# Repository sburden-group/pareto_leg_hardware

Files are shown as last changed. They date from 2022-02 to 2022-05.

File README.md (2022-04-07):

# Pareto Leg Hardware

contains all hardware (and control software) designs for the Pareto Leg

## Setup
Getting your environment ready to talk to some robot legs will involve:
1. provisioning your computer
1. provisioning the ODrive with the right firmware
1. calibrating the ODrive motors
1. Assembling the leg hardware
1. Wiring the leg electronics
1. Setting the zero point for each leg element

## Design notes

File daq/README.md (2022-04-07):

The "DAQ" is a separate device for measuring current.
It is installed in series into the power supply of the source (ODrive board in this case) to be measured.
Data is sampled at 5[KHz] and streamed in real time to a python script, which aggregates the data and writes it to a CSV file.

The DAQ is just a 1bitsy and a [ACHS-7124](https://www.pololu.com/product/4033)an analog in-series current measurement sensor.
A voltage divider that maps the input from 0-to-5 to 0-to-3.3 is also present.

## Usage

To start collecting data, use the **acquire\_data.py** script.
````
./acquire_data.py --seconds=3
````

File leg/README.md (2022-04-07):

# Pareto Leg Hardware
This is a CAD snapshot (Solidworks 2020) of the Pareto Leg.

## Summary
This model is modeled "[Top-Down](https://help.solidworks.com/2018/english/SolidWorks/sldworks/c_Top-Down_Design_Overview.htm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,moves%20down%20to%20the%20parts.)," where most of the structural parts are driven from parameters in *main\_body\_sketch.SLDPRT*.
The advantage is that variables can be tweaked from one file, and the rest of the top assembly will resize to accommodate the changes.
The top assembly also contains several *Configurations* with predefined parameters that will resize the model to create a particular leg instance.

If you need to make model changes, follow the guidelines in [editng_the_cads.md](./editing_the_cads.md)

# Fabrication Notes

## Fabrication Tools
* Drill Press
* 7mm Carbide Drill bit, [McMaster-Carr](https://www.mcmaster.com/3030A34/)
* Handheld Pipe Cutter, [McMaster-Carr option](https://www.mcmaster.com/pipe-cutters/metal-tube-and-conduit-cutters-8/)
* Soldering iron (for installing heat set inserts)
* Soldering iron Heat Set Insert Installation Tip, [Amazon](https://www.amazon.com/Heat-Set-Inserts-Compatible-SP40NKUS-Connecting/dp/B08B17VQLD)

## Stainless Steel Parts
Flat stainless steel parts (spring anchors) need to be sourced externally.
All spring anchors can be fabricated externally from [SendCutSend](https://sendcutsend.com/).
Simply import a DXF and specify *0.8mm thick 304 Stainless Steel* as the material.
(Pricing is ~$30 for about 10 spring anchors, and turnaround time is about 1 week.)

## Carbon Fiber Parts
Carbon Fiber Parts need to be sourced externally.
All carbon fiber parts can be fabricated externally from [CNCMadness.com](https://cncmadness.com/).
Just send him a DXF and specify *6mm plain weave carbon fiber*.
(Pricing is < $200 for two leg setups, and turnaround time is about 1 week.)

### Post-Processing
Parts from CNC Madness will need to be touched up before they can be used.
Specifically, the holes need to be cleaned up with a 7mm drill bit and a 5mm bushin needs to be installed in each joint hole.

### Warnings:
Carbon fiber is both sharp and very abrasive.
It can be wet-sanded to reduce the risk of injuring people who run their hands along the edge.
You must use carbide tooling to work with carbon fiber.
Conventional high speed steel tools will dull immediately.

## 3D Printed Parts

### Printed Part Settings
Print the following parts with these settings.
Note that exceptions exist, though.
See the notes for exceptions to these settings.

* 0.2mm or 0.24mm thick layer lines
* PLA or HTPLA
* print in the provided STL orientations
* 6 perimeter layers (This is critical especially for parts with inserts)
* No support material

| **Qty** | **Part Link** | **Notes** |
|:---:|:---:|:---:|
| 1 | [Foot](./fabrication_exports/stls/foot.STL) | Print with ~20 perimeter layers to create a solid object. Print from something more impact resistant than PLA, perhaps [CF HTPLA](https://www.proto-pasta.com/products/light-grey-carbon-fiber-composite-htpla). |
| 1 | [Threaded Foot Tip](./fabrication_exports/stls/threaded_foot_tip.STL) | Print from TPU or something rubbery |
| 2 | [Knee Bumper](./fabrication_exports/stls/knee_bumpter.STL) | |
| 2 | [Pogo Bearing Spacer](./fabrication_exports/stls/pogo_bearing_spacer.STL) | |
| 2 | [Knee Spring Anchor](./fabrication_exports/stls/knee_bumper.STL) | |
| 2 | [Pogo Center Tabs](./fabrication_exports/stls/pogo_center_tab.STL) | |
| 2 | [Pogo Center Tube Retainer](./fabrication_exports/stls/pogo_center_tube_retainer.STL) | can also be laser cut from 3.175mm Delrin sheet |
| 2 | [Inc Encoder Shaft Adaptor](./fabrication_exports/stls/inc_encoder_shaft_adaptor.STL) | can also be laser cut from 3.175mm Delrin sheet. Only needed if using AMT102-V encoders. |
| 2 | [Inc Encoder Shaft](./fabrication_exports/stls/incremental_encoder_shaft.STL) | Print *with* support material. Only needed if using AMT102-V encoders. |
| 8 | [M3 8mm Spacer](./fabrication_exports/stls/8mm_m3_spacer.STL) | |
| 1 | [Base Plate](./fabrication_exports/stls/base_plate.STL) or [No-Knee Springs Base Plate](./fabrication_exports/stls/base_plate_no_knee_springs.STL) | two different sizes depending on if the design uses knee springs or not. |

### Post Processing
The Foot Piece needs to have its 7mm hole drilled out, and then two 5mm bushing need to be pressed in, one from either end.
(You can use the same 7mm carbon fiber drill bit also used on the carbon fiber parts.)

## (3D Printed) Parts with Inserts
Some parts need heat-set inserts installed into them.
To install these, use a soldering iron with a heat-set insert tip and follow the [plate press technique](https://hackaday.com/2019/02/28/threading-3d-printed-parts-how-to-use-heat-set-inserts/).
Doing so should yield excellent surface finish with minimal blobbing.
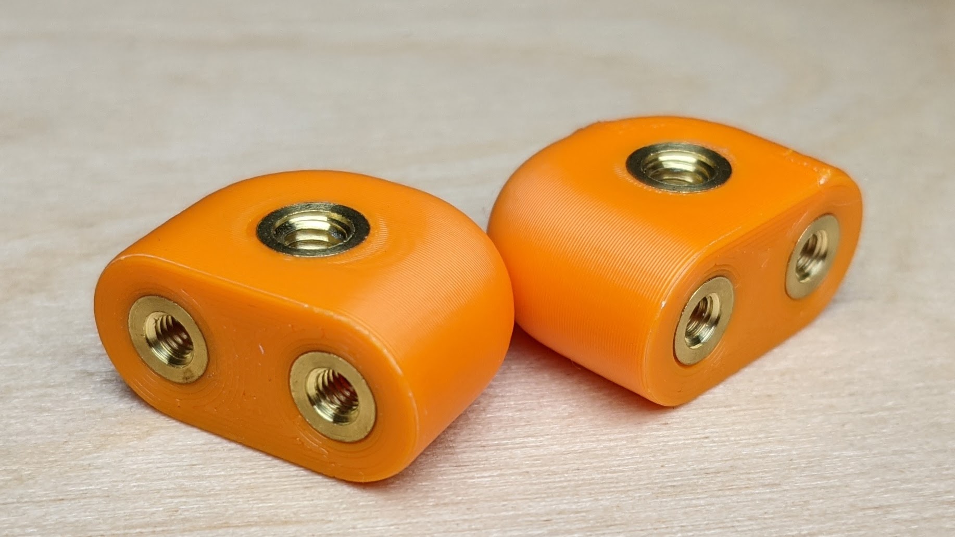
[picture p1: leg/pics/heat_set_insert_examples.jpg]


## Stainless Steel Guide Tube
This thin-walled tube comes from McMaster-Carr and can be cut to length with a pipe cutter. Length varies depending on design.
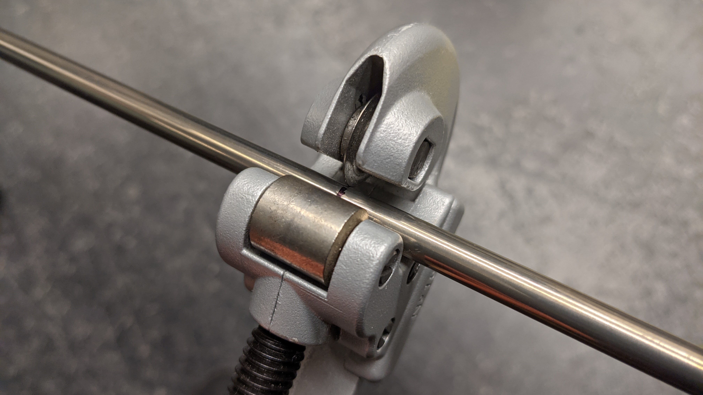
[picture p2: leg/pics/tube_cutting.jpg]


# Assembly
These robot legs can be assembled by you (or by some eager mechanically-curious undergrads).
For some of the finer details of the leg joint assembly, see [this doc](./knee_assembly_details.pdf).
For ordering more parts, see the [BOM](https://github.com/sburden-group/pareto_leg_hardware/blob/main/leg/no_spring_leg_bom%20L.pdf).

## Assembly Tools
You will need:
* 2mm Ball End Hex Key, [McMaster-Carr](https://www.mcmaster.com/5497A52/)
* 2.5mm Ball End Hex Key, [McMaster-Carr](https://www.mcmaster.com/5497A53/)
* 3mm Ball End Hex Key, [McMaster-Carr](https://www.mcmaster.com/5497A54/)
* 7mm Hex Nut Driver, [Amazon](https://www.amazon.com/gp/product/B000BQJ5ZY)

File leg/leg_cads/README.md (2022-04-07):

# CADs

This is a parametric assembly made with Solidworks 2020.
These files were exported with Solidworks' "Pack and Go" feature.

See the Assembly docs for info on sourcing stock parts, fabrication, and assembly.

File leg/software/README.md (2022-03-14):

## Folders
**Bringup Scripts** is for provisioning a new ODrive.

**lab\_experiments** is a "sketchbook" space for running lab experiments as scripts.

**leg\_control\_software** is the python package that enables control for the ODrive

**pareto-leg-control** is a Julia package for imposing particular dynamics on the robot in a control loop.

## Setup
**pareto-leg-control** is a separate Julia package with Python bindings installed as a submodule.
If you do not see it present as a directory, you need to download it with `git submodule init` followed by `git submodule update`.i

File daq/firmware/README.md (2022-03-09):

# Setup

## Required Hardware:
* breadboard
* [1bitsy](https://1bitsquared.com/products/1bitsy)
* [Black Magic Probe](https://www.adafruit.com/product/3839) for flashing
* Pololu In-Line Current Sensor, [+/- 40A](https://www.pololu.com/product/4033)

## Linux Development and Compiling Setup
* add the udev rules for (1) the black magic probe, (2) the 1bitsy custom usb device to your */etc/udev/rules.d* folder and then reload rules with `sudo udevadm control reload-rules`.
* Install gcc-arm-embedded according to the [libopencm3 guide](https://github.com/libopencm3/libopencm3#prerequisites)
* Pull the submodule repository in with: `git submodule init` and then `git submodule update`.
* cd into the **libopencm3** directory and build the code with `make`
* with libopencm3 built, you can now invoke the Makefile for this project in this directory with `make`

### Flashing
With the code compiled, you should be able to flash it with `make bmp-flash`.

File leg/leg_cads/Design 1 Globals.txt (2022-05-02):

"l2" = 191

"D3@Body Driving Dimensions" = "l2"

"l1" = 104

"D4@Body Driving Dimensions" = "l1"

"s1r" = 135deg

"s2r" = - 135deg

"offset"= 10mm

"s1_len" = 0mm

"s2_len" = 0mm

"s1_anchor_dist"= "offset" + "l1" + "s1_len"

"s2_anchor_dist"= "offset" + "l1" + "s2_len"'this was: = "offset" + "l1" + "s2_len"

"D5@Body Driving Dimensions" = "s1_anchor_dist"

"D6@Body Driving Dimensions" = "s2_anchor_dist"

"D7@Body Driving Dimensions" = "s1r"

"D8@Body Driving Dimensions" =  - "s2r"

"carbon_fiber_plate_thickness"=6

"motor_to_motor_spacing"=55.5

"D1@Sketch4"="motor_to_motor_spacing"

"D1@Boss-Extrude3"="l1"+"l2" + 8

"D1"= "motor_to_motor_spacing" + 30mm

"D10@Body Driving Dimensions"="offset"+5mm

"D12@Body Driving Dimensions"="offset"+5mm

"D4@side plate profile"="l1"+"offset"

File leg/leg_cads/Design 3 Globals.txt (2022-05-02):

"l2" = 182.421

"l1" = 87.579

"s1r" = 2.356194rad

"s2r"= - 135deg

"offset"= 10mm

"s1_len" = 76.2mm

"s2_len" = 0mm

"s1_anchor_dist"= "offset" + "l1" + "s1_len"

"s2_anchor_dist"= "offset" + "l1" + "s2_len"'this was: = "offset" + "l1" + "s2_len"

"carbon_fiber_plate_thickness"=6

"motor_to_motor_spacing"=55.5

"D1"= "motor_to_motor_spacing" + 30mm

"pogo_spacer_offset"= 15mm + 6.38mm

"cspring len" = 116.586

"cspring mult" = 2

"cspring_spacer_depth"= "l1" + "l2" - "cspring len" * "cspring mult" - "pogo_spacer_offset"

"D1@Boss-Extrude1"="cspring_spacer_depth"

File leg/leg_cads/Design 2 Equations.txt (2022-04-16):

"l2"= 185

"D3@Body Driving Dimensions" = "l2"

"l1"= 85

"D4@Body Driving Dimensions" = "l1"

"s1r"= 2.14212rad

"s2r"= - 2rad

"offset"= 15mm

"s1_len"= 0.08255m

"s2_len"= 0.015m

"s1_anchor_dist"= "offset" + "l1" + "s1_len"

"s2_anchor_dist"= "offset" + "l1" + "s2_len"'this was: = "offset" + "l1" + "s2_len"

"D5@Body Driving Dimensions" = "s1_anchor_dist"

"D6@Body Driving Dimensions" = "s2_anchor_dist"

"D7@Body Driving Dimensions" = "s1r"

"D8@Body Driving Dimensions" =  - "s2r"

"carbon_fiber_plate_thickness"=6

"D1@Tibya" = "carbon_fiber_plate_thickness"

"D1@Boss-Extrude2"="carbon_fiber_plate_thickness"

"motor_to_motor_spacing"=55.5

"D1@Sketch4"="motor_to_motor_spacing"

"D1@Boss-Extrude3"="l1"+"l2" + 8

"D1" = "motor_to_motor_spacing" + 30mm

"D1@Boss-Extrude12"="carbon_fiber_plate_thickness"

"D3@Sketch44"="s2_anchor_dist"/2

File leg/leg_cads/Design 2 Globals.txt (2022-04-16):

"l2"= 185

"l1"= 85

"s1r"= 2.14212rad

"s2r"= - 2rad

"offset"= 10mm

"s1_len"= 0.08255m

"s2_len"= 0.015m

"s1_anchor_dist"= "offset" + "l1" + "s1_len"

"s2_anchor_dist"= "offset" + "l1" + "s2_len"'this was: = "offset" + "l1" + "s2_len"

"carbon_fiber_plate_thickness"=6

"motor_to_motor_spacing"=55.5

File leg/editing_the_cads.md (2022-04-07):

# Editing The Model

Here's a quick walkthrough on exporting leg assemblies with custom dimenionsions.

## Configuraiton Overview
Many parts in the assembly are driven from a single part (`main_body_sketch.SLDPRT`) with many configurations, each of which has parameters set to different values.
The assembly itself also several configurations, each of which represent a different leg designs at a particular point in the design space.
This assembly configuration is built from parts pinned to a particular configuration.

## Tweaking Existing Leg Designs
Four Leg designs exist as separate configurations in the top assembly.

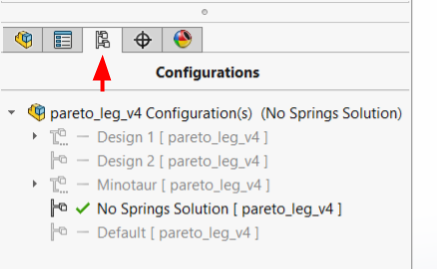
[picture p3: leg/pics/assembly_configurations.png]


To tweak an existing design's parameters, start by opening `main_body_sketch.SLDPRT`. Note that this part has configurations with names that match that of the corresponding assembly configuration.
To edit the equations that drive any configuration, right-click on *Equations* in the feature tree and select *Manage Equations*.

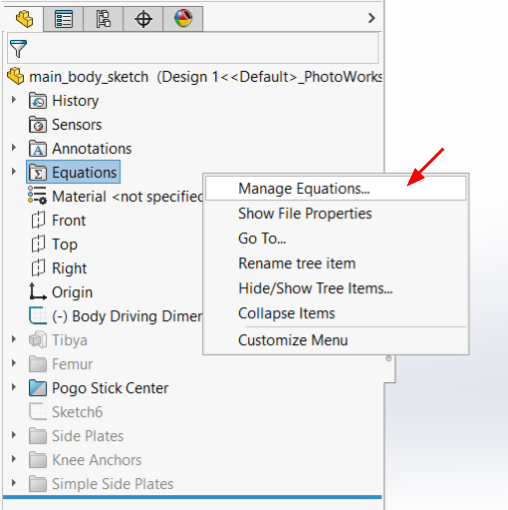
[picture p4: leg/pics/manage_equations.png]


This new window gives you direct edit access to parameters that drive the model.
Note that these parameters can be made to apply globally or be configuration-specific.
In pretty-much all cases, we want our parameter values to apply to be configuration-specific.

To edit a parameter, first ensure that the desired configuration is selected in the upper right corner and make sure that the variable value scope is set to *This Configuration*.

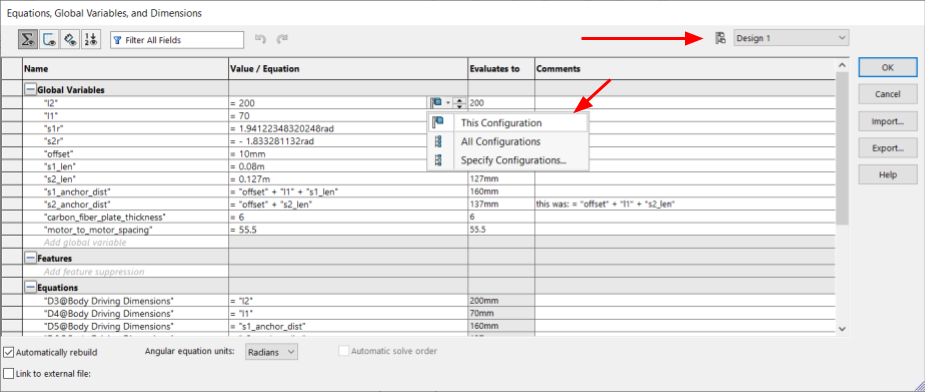
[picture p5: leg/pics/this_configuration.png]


Now you can just check *OK*, and the model configuration, and all derived configurations will apply the new value.
At this point, if you have the assembly open, it should prompt you about rebuilding the model.
If you say yes, the parts will resize.
If you save `main_body_sketch.SLDPRT`, these changes will take effect.

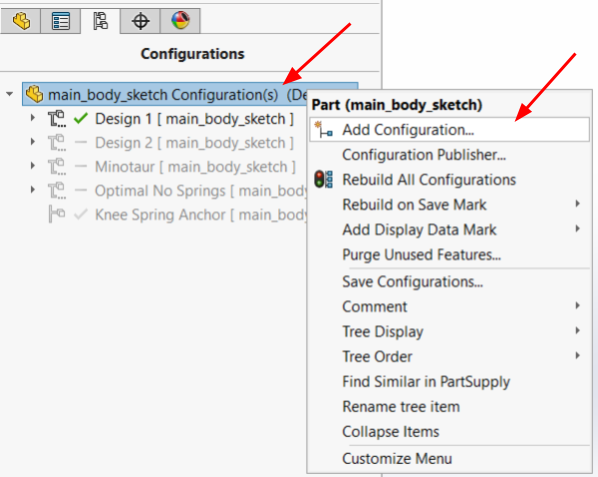
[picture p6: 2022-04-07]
leg/pics/new_configuration_part_level.png

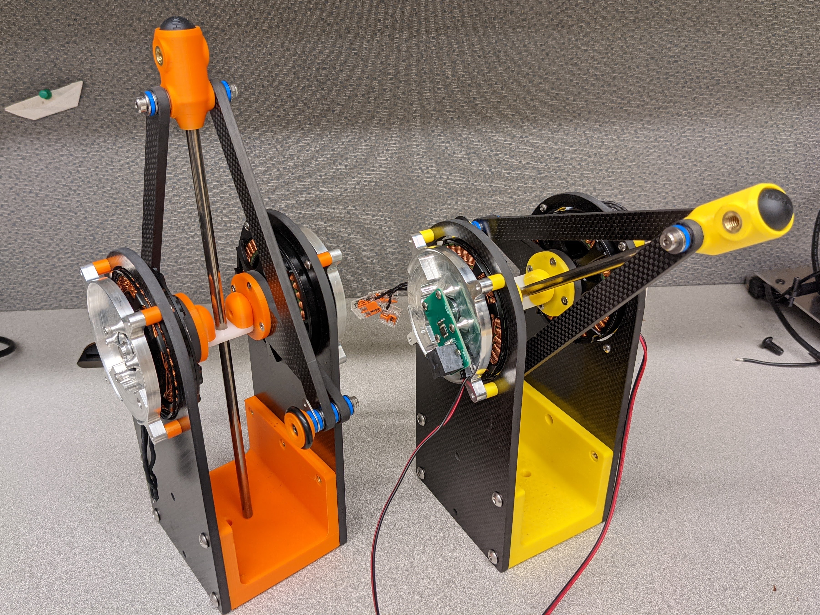
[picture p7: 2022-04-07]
leg/pics/pareto_leg_samples.jpg

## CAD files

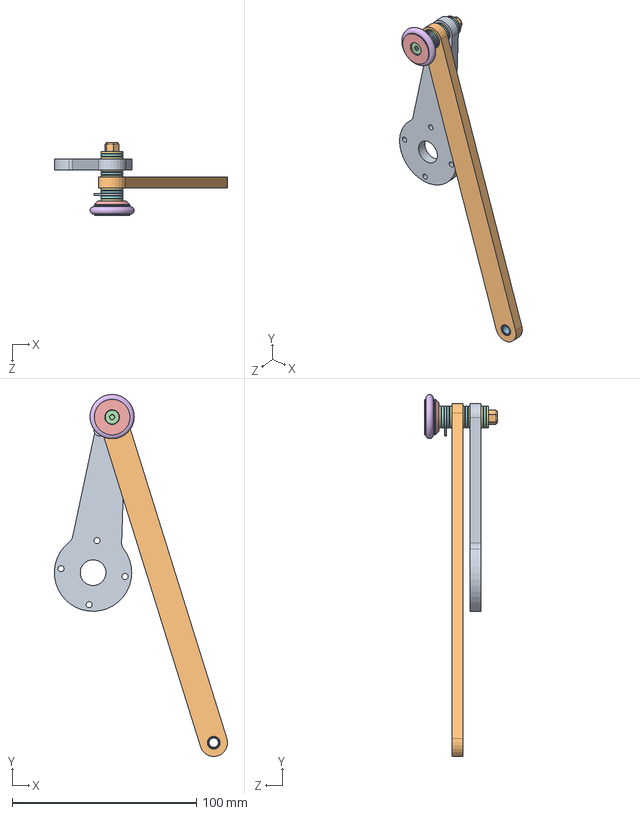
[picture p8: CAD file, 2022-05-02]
leg/leg_cads/half leg assembly v5.SLDASM
93.9 x 196.4 x 39.8 mm
Femur V5
Tibia v5
5mm_sleeve_bearing_6mm_long_7mm_od_MDZB5-6 x 3
m4_shoulder_screw_5mm_d_30mm_l_90278A376
knee_bumper_v4
9262K342-o-ring
m5_shim_1mm_thick_PCIMR5-12-1.0 x 6
thrust_bearing_5mm_bore_mtb-0512 x 4
Knee Anchor Loop
m4_locknut_93625A150

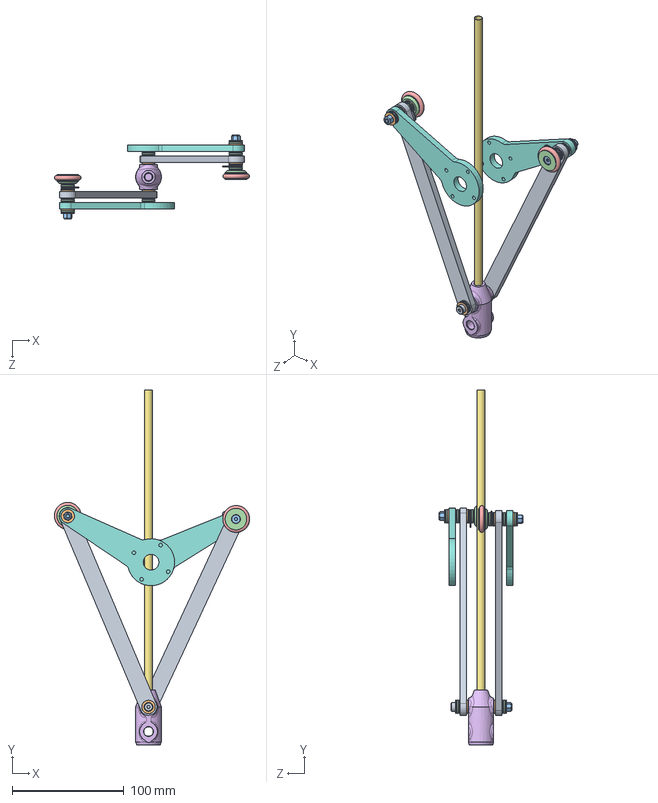
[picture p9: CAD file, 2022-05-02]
leg/leg_cads/full leg assembly v5.SLDASM
174.4 x 317.0 x 75.3 mm
m4_shoulder_screw_5mm_d_45mm_l_90278A507
m5_shim_1mm_thick_PCIMR5-12-1.0 x 18
m4_locknut_93625A150 x 3
thrust_bearing_5mm_bore_mtb-0512 x 10
5x11x4_flanged_bearing_57155K571 x 2
foot_v4
Pogo stick v5
Femur V5 x 2
Tibia v5 x 2
5mm_sleeve_bearing_6mm_long_7mm_od_MDZB5-6 x 6
m4_shoulder_screw_5mm_d_30mm_l_90278A376 x 2
knee_bumper_v4 x 2
9262K342-o-ring x 2
Knee Anchor Loop x 2

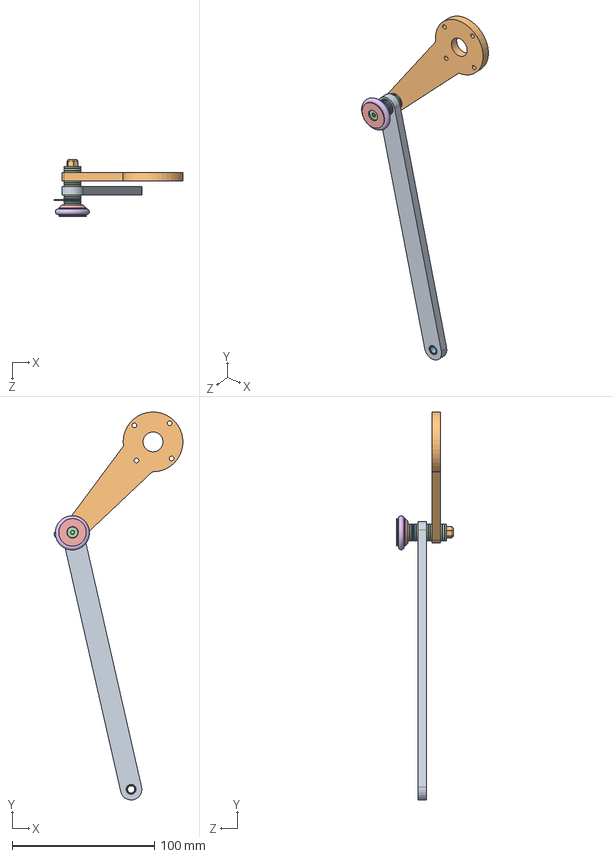
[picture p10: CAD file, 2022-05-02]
leg/leg_cads/Leg Assembly V5.SLDASM
90.3 x 272.4 x 39.8 mm
Femur V5
Tibia v5
5mm_sleeve_bearing_6mm_long_7mm_od_MDZB5-6 x 3
m4_shoulder_screw_5mm_d_30mm_l_90278A376
knee_bumper_v4
9262K342-o-ring
m5_shim_1mm_thick_PCIMR5-12-1.0 x 6
thrust_bearing_5mm_bore_mtb-0512 x 4
Knee Anchor Loop
m4_locknut_93625A150

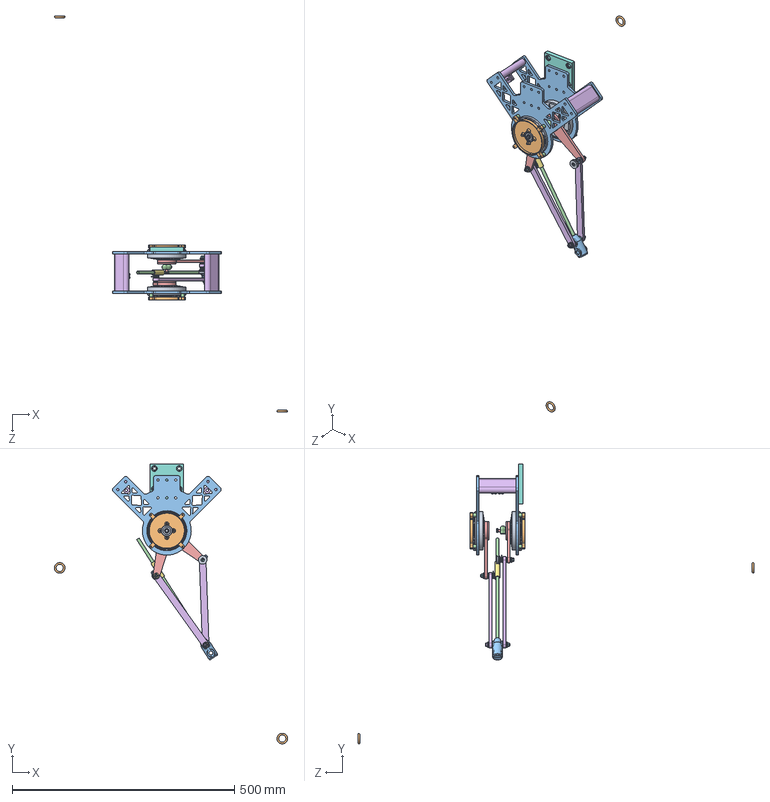
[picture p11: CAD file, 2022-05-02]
leg/leg_cads/Full Robot Assembly V5.SLDASM
524.9 x 629.8 x 891.1 mm
DYS 8108 x 2
motor_plate x 2
Side plate v5 x 2
8mm_spacer x 8
pogo_bearing_spacer x 2
m4_shoulder_screw_5mm_d_45mm_l_90278A507
m5_shim_1mm_thick_PCIMR5-12-1.0 x 18
m4_locknut_93625A150 x 3
thrust_bearing_5mm_bore_mtb-0512 x 10
5x11x4_flanged_bearing_57155K571 x 4
foot_v4
Pogo stick v5
Femur V5 x 2
Tibia v5 x 2
5mm_sleeve_bearing_6mm_long_7mm_od_MDZB5-6 x 6
m4_shoulder_screw_5mm_d_30mm_l_90278A376 x 2
knee_bumper_v4 x 2
9262K342-o-ring x 2
Knee Anchor Loop x 2
pogo_center
m4_shoulder_screw_5mm_d_5mm_l_90265A126 x 2
Knee Anchor V5 x 2
cspring_spacer
mounting bracket

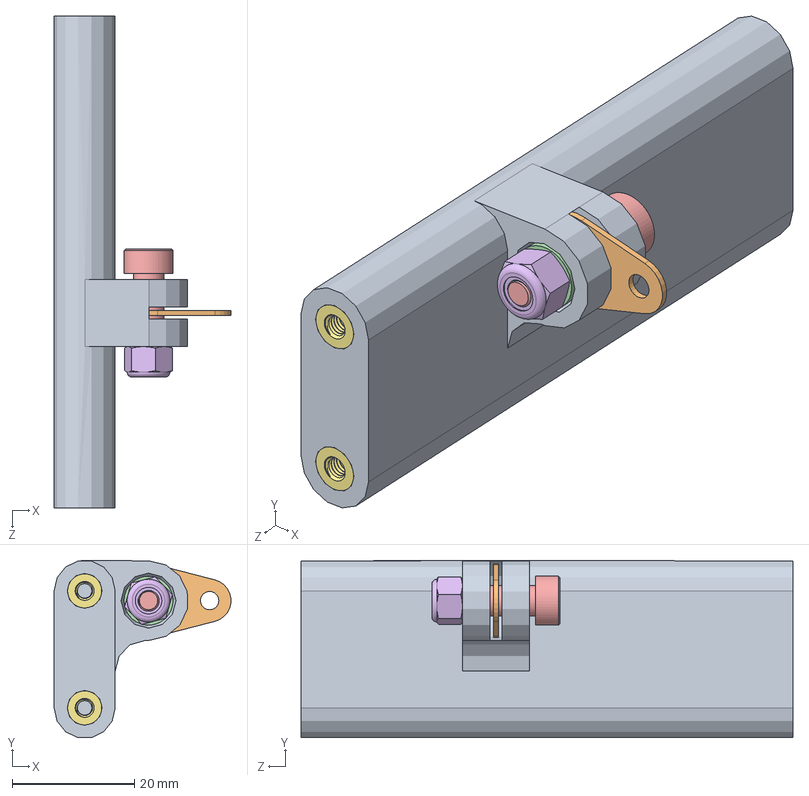
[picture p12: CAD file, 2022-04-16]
leg/leg_cads/knee_anchor_assembly.SLDASM
28.9 x 29.0 x 80.5 mm
main_body_sketch
knee_spring_anchor
4mm_sleeve_bearing_3mm_long_8mm_od_6658K114
5mm_sleeve_bearing_4mm_long_8mm_od_6658K116
m4_shoulder_screw_5mm_d_12mm_l_90278A371
m4_locknut_93625A150
m3_heat_set_insert_94180A331 x 4

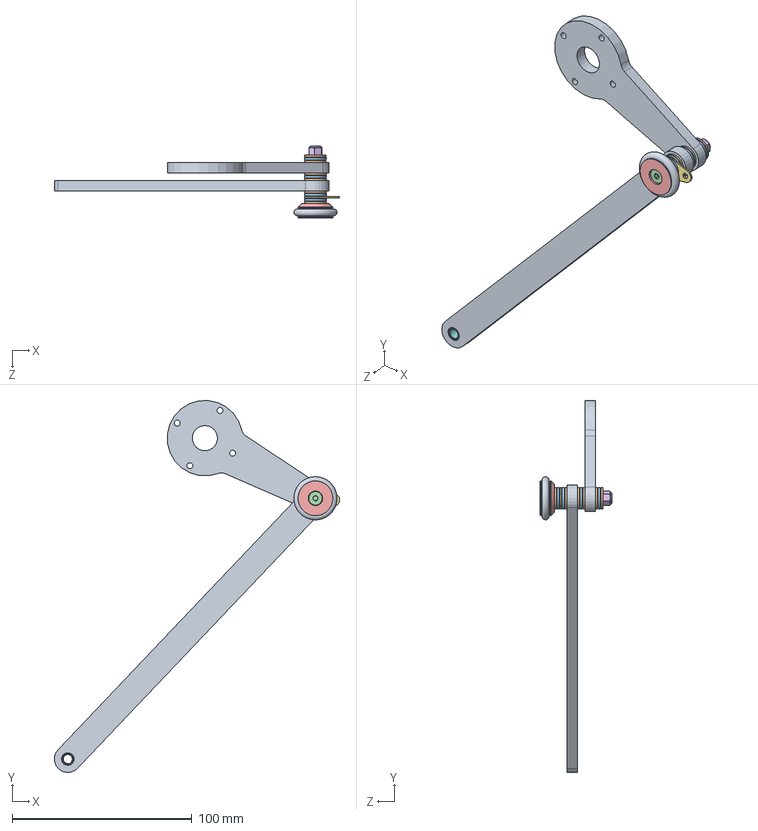
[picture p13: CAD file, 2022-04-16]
leg/leg_cads/leg_assembly.SLDASM
158.7 x 206.9 x 39.8 mm
main_body_sketch x 2
m5_shim_1mm_thick_PCIMR5-12-1.0 x 6
thrust_bearing_5mm_bore_mtb-0512 x 4
m4_shoulder_screw_5mm_d_30mm_l_90278A376
knee_bumper_v4
m4_locknut_93625A150
knee_spring_anchor
5mm_sleeve_bearing_6mm_long_7mm_od_MDZB5-6 x 3
9262K342-o-ring

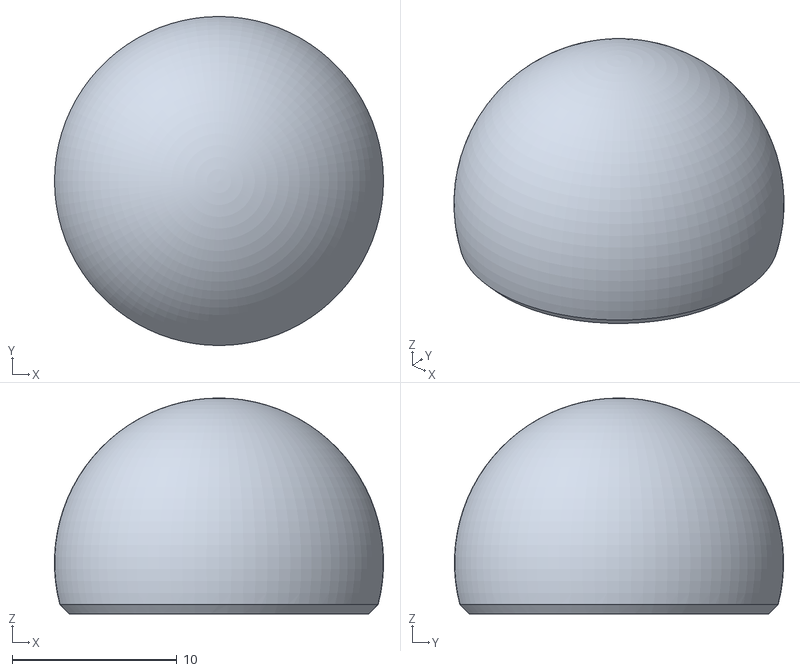
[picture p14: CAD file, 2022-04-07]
leg/fabrication_exports/stls/threaded_foot_tip.STL
20.0 x 20.0 x 13.1

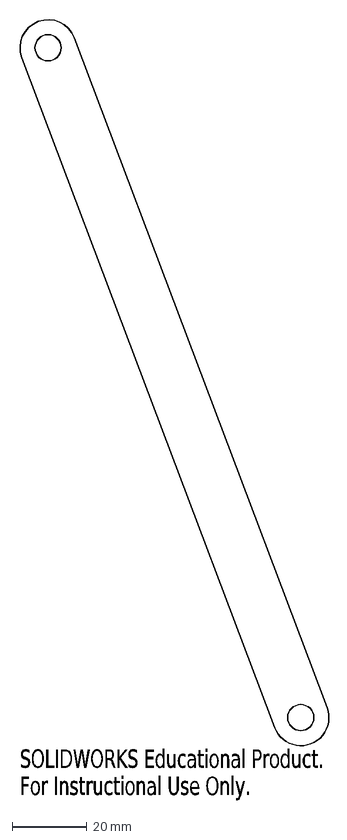
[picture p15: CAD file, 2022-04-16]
leg/leg_cads/outputs/design 1/tibia_1.DXF
SOLIDWORKS Educational Product.
For Instructional Use Only.

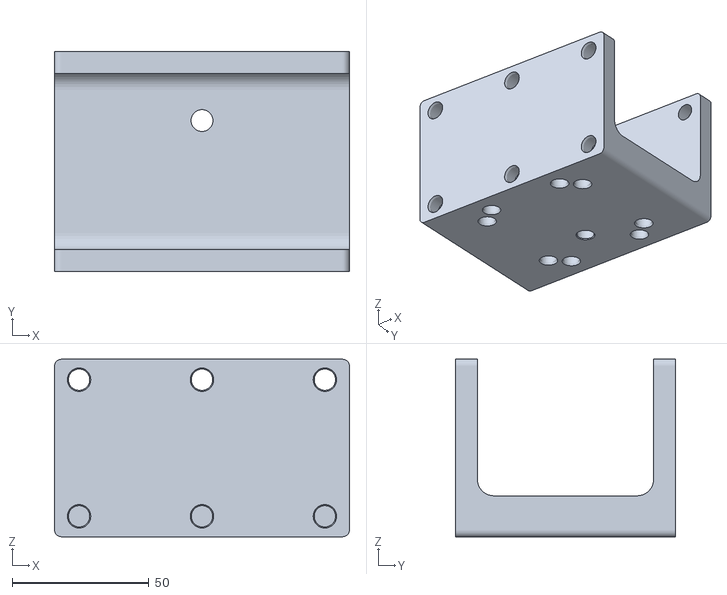
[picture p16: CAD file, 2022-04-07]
leg/fabrication_exports/stls/base_plate_no_knee_springs.STL
108.0 x 80.5 x 65.0

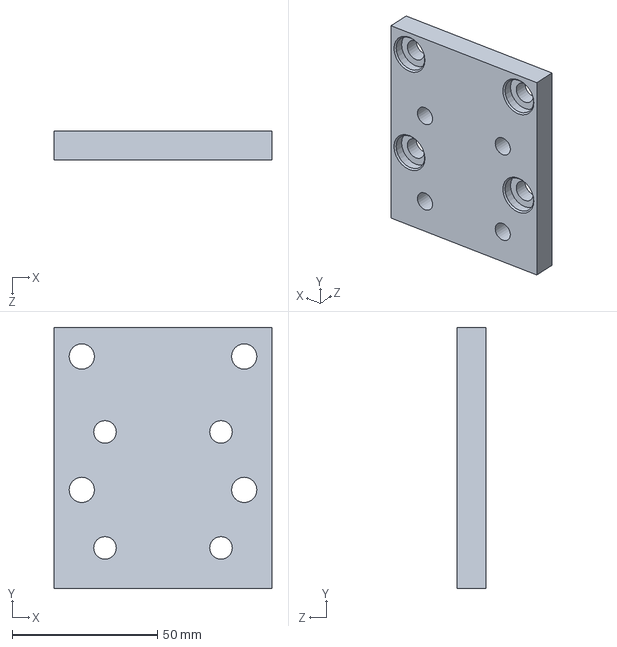
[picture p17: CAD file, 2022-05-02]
leg/leg_cads/mounting bracket.SLDPRT
75.0 x 90.0 x 10.0 mm

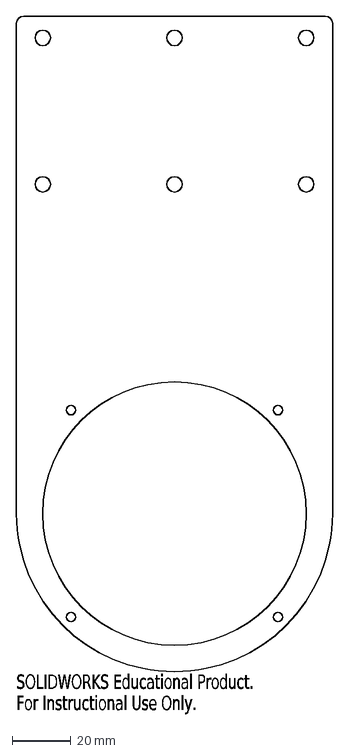
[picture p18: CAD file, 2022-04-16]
leg/leg_cads/outputs/design 1/sideplate_1.DXF
SOLIDWORKS Educational Product.
For Instructional Use Only.

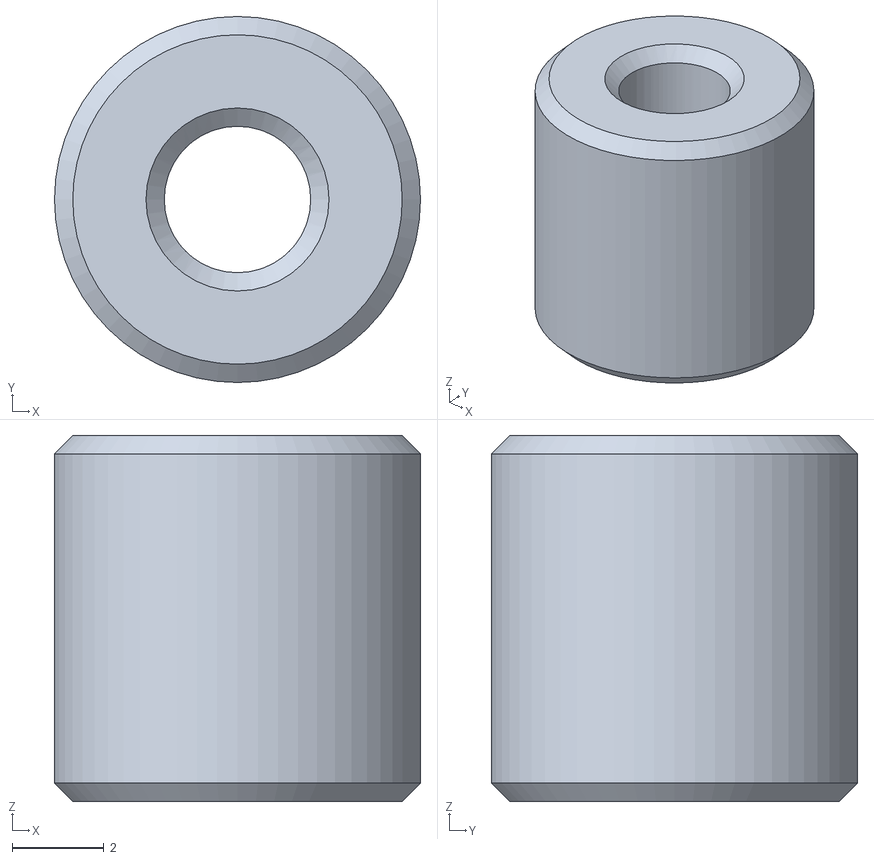
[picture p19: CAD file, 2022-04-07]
leg/fabrication_exports/stls/8mm_m3_spacer.STL
8.00 x 8.00 x 8.00

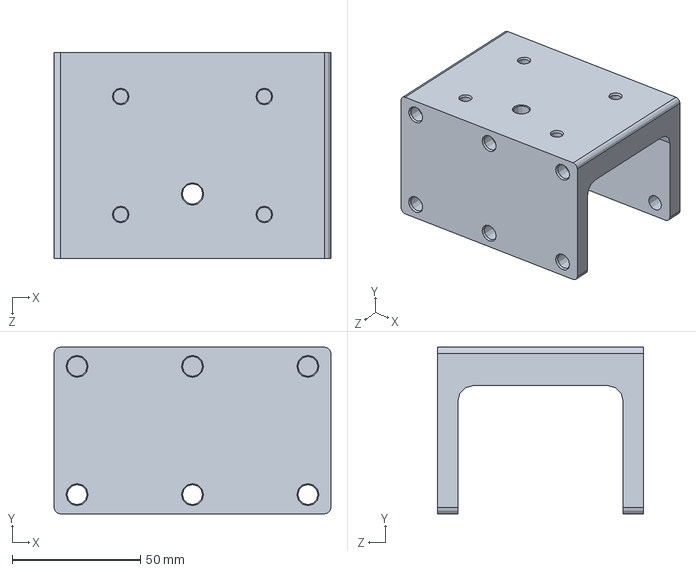
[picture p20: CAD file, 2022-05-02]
leg/leg_cads/base_plate.SLDPRT
108.0 x 65.0 x 80.5 mm

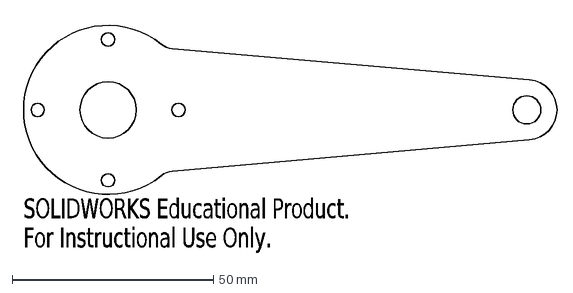
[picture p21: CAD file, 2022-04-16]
leg/leg_cads/outputs/design 1/femur_1.DXF
SOLIDWORKS Educational Product.
For Instructional Use Only.

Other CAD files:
leg/leg_cads/main_body_sketch.SLDPRT
leg/fabrication_exports/stls/incremental_encoder_shaft.STL
leg/leg_cads/Knee Anchor Loop.SLDPRT
leg/fabrication_exports/stls/base_plate.STL
leg/fabrication_exports/stls/foot.STL
leg/fabrication_exports/stls/inc_encoder_shaft_adaptor.STL
leg/fabrication_exports/stls/knee_bumper.STL
leg/fabrication_exports/stls/knee_spring_anchor.STL
leg/fabrication_exports/stls/pogo_bearing_spacer.STL
leg/fabrication_exports/stls/pogo_center_tab.STL
leg/fabrication_exports/stls/pogo_center_tube_retainer.STL
leg/leg_cads/4mm_sleeve_bearing_3mm_long_8mm_od_6658K114.SLDPRT
leg/leg_cads/5mm_sleeve_bearing_4mm_long_8mm_od_6658K116.SLDPRT
leg/leg_cads/5mm_sleeve_bearing_6mm_long_7mm_od_MDZB5-6.SLDPRT
leg/leg_cads/5x11x4_flanged_bearing_57155K571.SLDPRT
leg/leg_cads/8mm_spacer.SLDPRT
leg/leg_cads/9262K342-o-ring.SLDPRT
leg/leg_cads/DYS 8108.SLDPRT
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

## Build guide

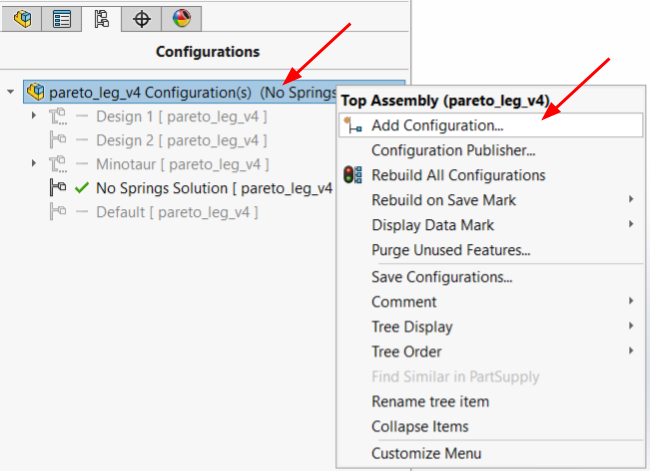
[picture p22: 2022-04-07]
leg/pics/new_configuration_assembly_level.png

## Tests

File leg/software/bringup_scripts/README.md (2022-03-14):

## Computer Environment Setup

1. Create a virtual environment - make sure the python package is not newer than 3.8.6
1. Enter that new environment
1. `pip install --upgrade odrive`

- manual setup: 'odrivetool'

## troubleshoot (windows)
- If getting error of "[USB] Could not open USB device: -5": download Zadig and replace the driver to libusb (v1.2.6.0 for me). (https://docs.odriverobotics.com/troubleshooting.html#usb-connectivity-issues)

## Hardware Troubleshooting
- Encoders need to be rebooted if you change the config, so everything needs to be power-cycled.
- Wait for the LED to burn out before turning power back on.

## Reflashing:
- in `tup.config`, board should be set to `CONFIG_BOARD_VERSION=v3.5-48V`
- To compile the firmware, invoke `make` from the top level directory.
- To flash the firmware, invoke `make dfu`.
If the flashing doesn't work, you may need to power the board up with the board's Dip switch set to DFU, invoke `make dfu`, and the flip the Dip switch back to RUN and reboot the board.

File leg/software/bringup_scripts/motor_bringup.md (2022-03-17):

# Bringup

Note: this process is kinda involved and should really be automated with a script.

Run the **odrivetool** utility.

Power up the PSU and apply 24V to the board.

Check that there are no errors with `dump_errors(odrv0)`.

If there are no errors, close the odrive utility.

run `bringup.py` to upload the Dual TMotor U8 motor configuration for each axis.

Reopen the odrive utility. Check that there no errrors with `dump_errors(odrv0)`.

Ensure that the motors are not connected to anything that would phyiscally constrain their movement (i.e: linkages).

Run a motor0 calibration with:
````
odrv0.axis0.requested_state = AXIS_STATE_FULL_CALIBRATION_SEQUENCE
````
When calibration finishes, check that there no errrors with `dump_errors(odrv0)`.

Run a motor1 calibration with:
````
odrv0.axis1.requested_state = AXIS_STATE_FULL_CALIBRATION_SEQUENCE
````
When calibration finishes, check that there no errrors with `dump_errors(odrv0)`.

If there are no errors, tell the motor to show up pre-calibrated by setting the following:

````
odrv0.axis0.motor.config.pre_calibrated = True
odrv0.axis0.encoder.config.pre_calibrated = True
odrv0.axis1.motor.config.pre_calibrated = True
odrv0.axis0.encoder.config.pre_calibrated = True
````

Now save the configuration with:
````
odrv0.save_configuration()
````

Close the odrive utility.

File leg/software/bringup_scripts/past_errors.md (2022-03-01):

# Past Errors

Here are some errors we have previously encountered.

* Before compiling and flashing custom firmware, check that the board versin in`tup.config` is set to the actual board we have in the lab. For reference, we have `CONFIG_BOARD_VERSION=v3.5-48v`
* Before flashing code, make sure the DIP switch is set to *DFU* on powerup.
* After flashing code, make sure that the DIP switch is set back to *RUN* on powerup.
* After flashing code, you need to reconfigure the robot with the bringup procedure.

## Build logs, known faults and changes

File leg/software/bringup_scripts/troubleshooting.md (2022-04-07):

# Troubleshooting

Here are some errors we have previously encountered.

* Before compiling and flashing custom firmware, check that the board versin in`tup.config` is set to the actual board we have in the lab. For reference, we have `CONFIG_BOARD_VERSION=v3.5-48v`
* Before flashing code, make sure the DIP switch is set to *DFU* on powerup.
* After flashing code, make sure that the DIP switch is set back to *RUN* on powerup.
* After flashing code, you need to reconfigure the robot with the bringup procedure.

## odrivetool Commands

Here are some useful commands that you can run with the odrive utility.

* `dump_errors(odrv0)` will dump the system state to the screen and display any errors in red.
* `odrv0.reboot()` will reboot the system

* `odrv0.axis0.encoder.shadow_count` read the raw AS5048A encoder count in ticks
* `odrv0.axis0.encoder.pos_estimate` read axis0 angle in rotations
* `odrv0.axis0.encoder.set_linear_count(0)` zero out the current angle of axis0.

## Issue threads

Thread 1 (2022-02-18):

General TODOs for Hardware Testing

Poofjunior, 2022-02-18:
## Hardware
### CAD
- [ ] Add strain relief for robot wires. (3D printed part)
### PCBs
- [ ] populate 8x encoder PCBs
- [ ] test them
### Wire Harnesses
- [ ] make 2m wire harnesses for each robot
-  [ ] order wire harness stuff
- [ ] longer ethernet cables (6 ft, very flexible)
- [ ] make encoder power harnesses (Molex Microfit 3.0)
#### label stuff
- [ ] label all phases (1, 2, 3) to match
- [ ] label motor wires (motor0 and motor1)
- [ ] label encoder RJ45 wires (axis0, axis1)
- [ ] label the robot's motors
### Test Rig
- [ ] get a mount for the odrive

## Conventions
- [ ] get a picture that defines conventions:
* motor 0
* motor 1
* positive theta rotation for motor 0
* positive theta rotation for motor 1

## Software
- [ ] write controller
- [ ] calibrate both motors.
- [ ] make both move without errors.

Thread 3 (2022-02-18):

Need Configuration Convention Picture

Poofjunior, 2022-02-18:
Looking at the robot from a side view:
* Motor 0 is closer to you
* leg end-effector CCW is positive
* Motor 0 "femur" "leads" in the CCW direction. (i.e: with the leg end-effector pointing straight down, Motor 0 femur is slightly positive and Motor 1 femur is slightly negative.)

Make a diagram that has all this stuff in it.

hachouuw, 2022-03-02:
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

hachouuw, 2022-03-03:
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

hachouuw, 2022-03-03:
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

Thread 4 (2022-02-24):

Current Measurements: Fix Sample Rate

Poofjunior, 2022-02-24:
Sampling rate on the 1Bitsy (STM32F415RGTx) currently needs to be fixed. It's sampling at who-knows-what rate right now.

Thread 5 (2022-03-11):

Apply Sign Flip in ODriveDriver

Poofjunior, 2022-03-11:

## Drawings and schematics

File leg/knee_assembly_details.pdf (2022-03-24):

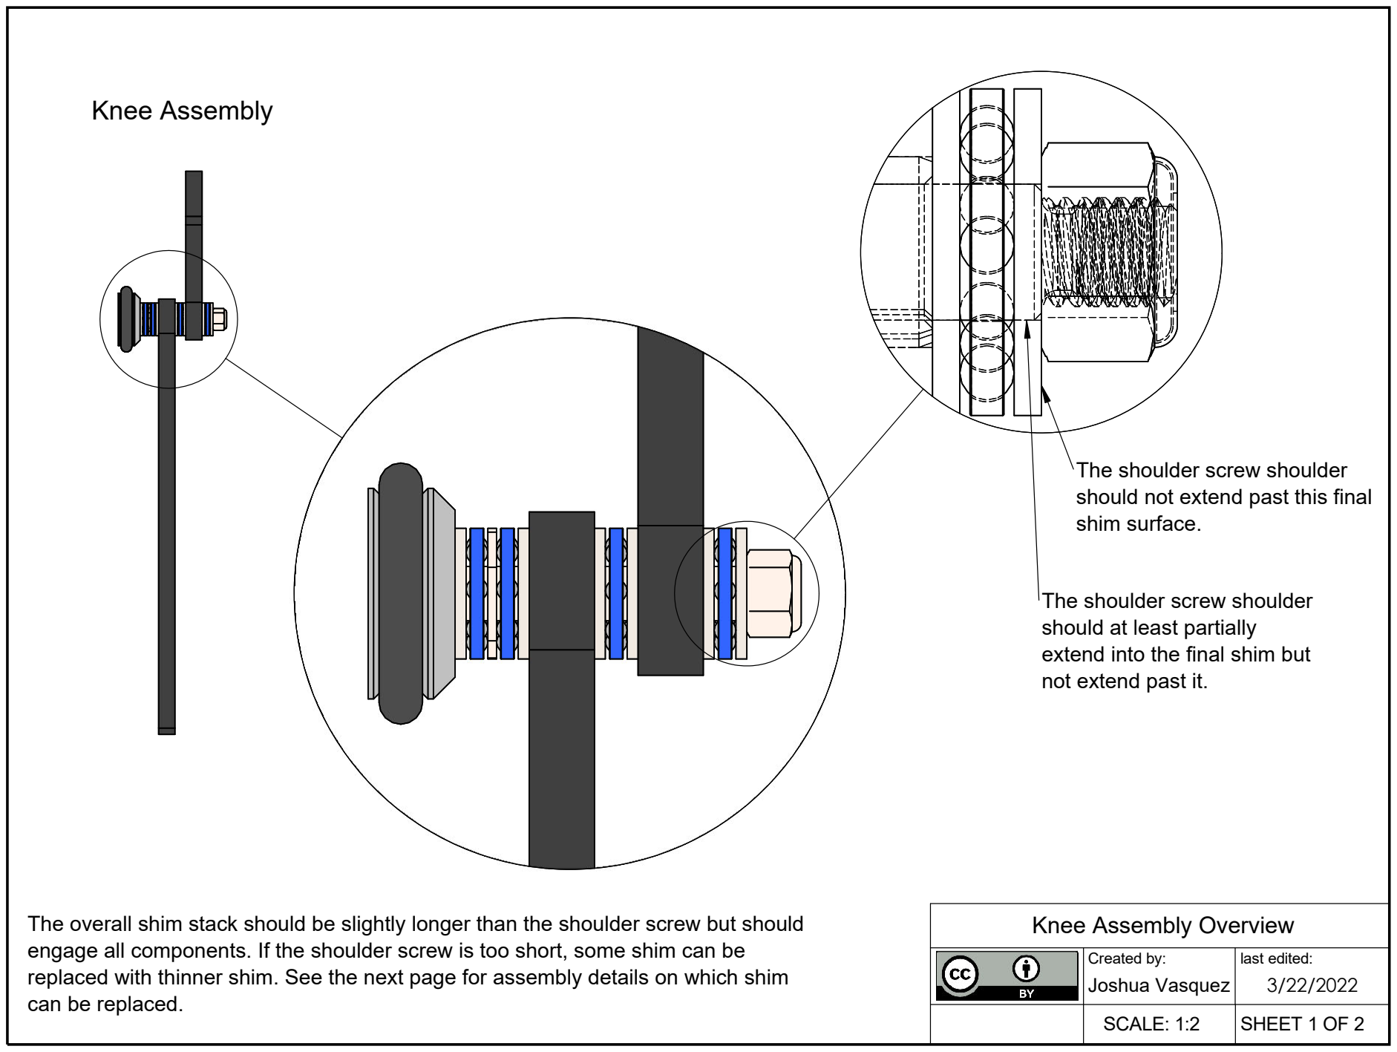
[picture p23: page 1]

The shoulder screw shoulder should not extend past this final shim surface.

The shoulder screw shoulder should at least partially
extend into the final shim but not extend past it.

3/22/2022

SHEET 1 OF 2

last edited:

SCALE: 1:2

Joshua Vasquez

Created by:

The overall shim stack should be slightly longer than the shoulder screw but should | Knee Assembly Overview
engage all components. If the shoulder screw is too short, some shim can be
replaced with thinner shim. See the next page for assembly details on which shim
can be replaced.

### Knee Assembly

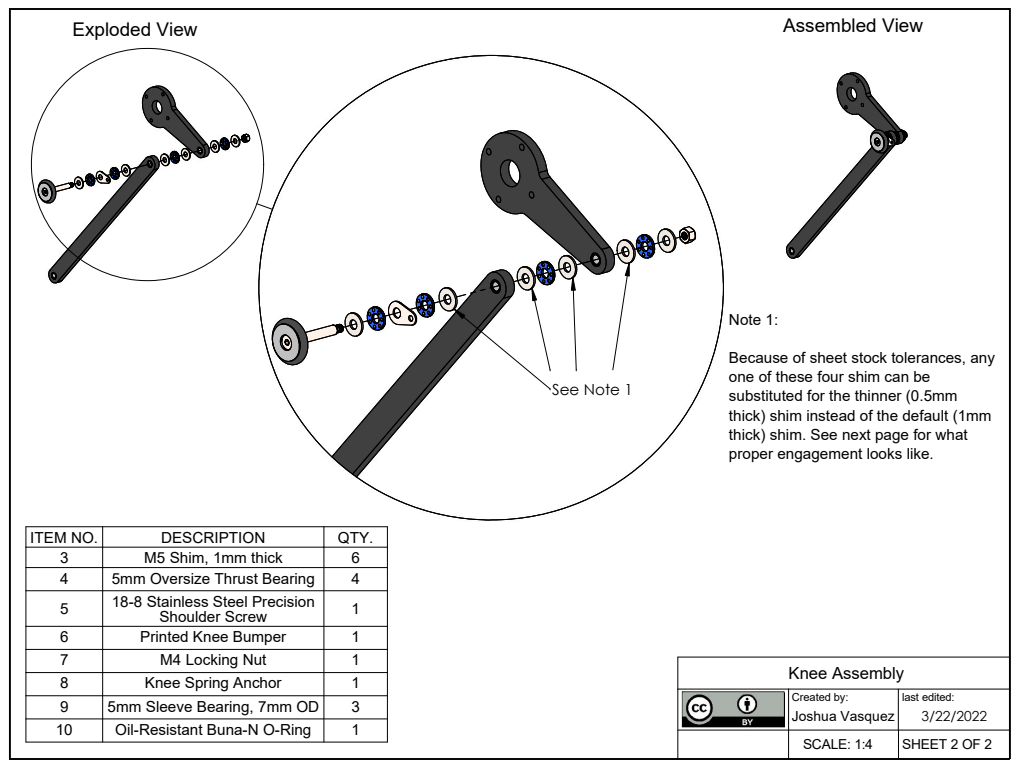
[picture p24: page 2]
See Note 1; Assembled View; Joshua Vasquez; Created by:; last edited:; SCALE: 1:4; SHEET 2 OF 2; Knee Assembly; Note 1:; Exploded View

Because of sheet stock tolerances, any
one of these four shim can be
substituted for the thinner (0.5mm
thick) shim instead of the default (1mm
thick) shim. See next page for what
proper engagement looks like.

ITEM NO. | DESCRIPTION | QTY.
3 | M5 Shim, 1mm thick | 6
4 | 5mm Oversize Thrust Bearing | 4
5 | 18-8 Stainless Steel Precision Shoulder Screw | 1

6 | Printed Knee Bumper | 1
7 | M4 Locking Nut | 1
8 | Knee Spring Anchor | 1
9 | 5mm Sleeve Bearing, 7mm OD | 3
10 | Oil-Resistant Buna-N O-Ring | 1

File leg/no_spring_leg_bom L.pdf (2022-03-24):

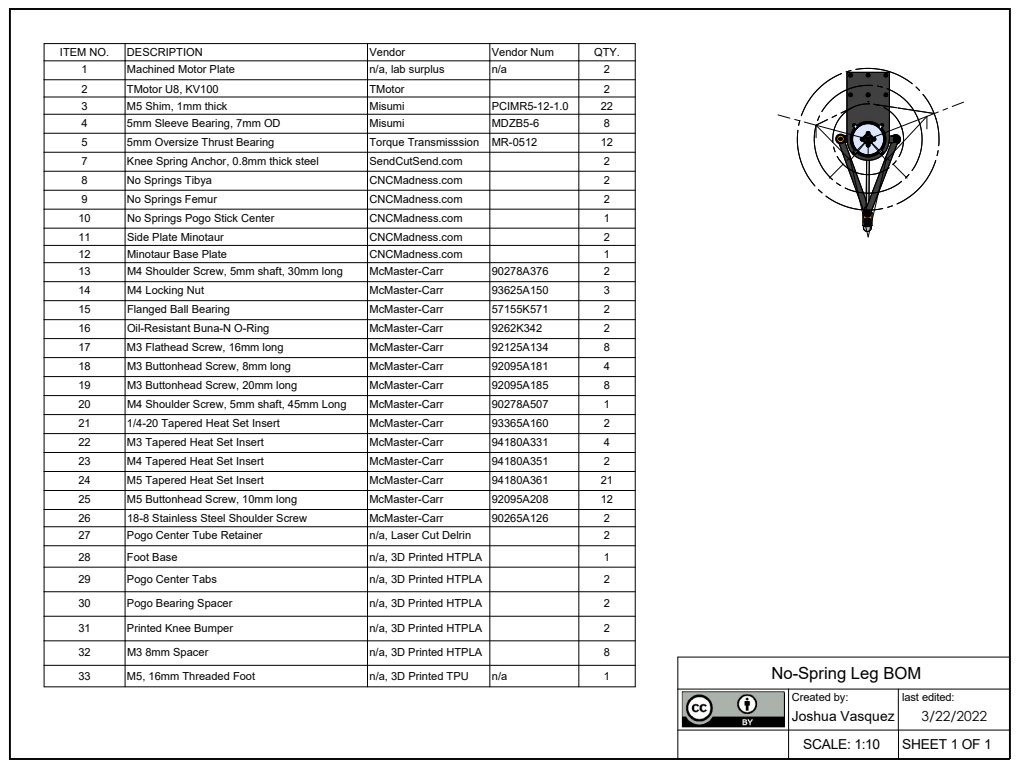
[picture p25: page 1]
last edited:; SHEET 1 OF 1; SCALE: 1:10; Joshua Vasquez; Created by:

ITEM NO. | DESCRIPTION | Vendor | Vendor Num | QTY.
1 | Machined Motor Plate | n/a, lab surplus | n/a | 2
2 | TMotor U8, KV100 | TMotor | | 2
3 | M5 Shim, 1mm thick | Misumi | PCIMR5-12-1.0 | 22
4 | 5mm Sleeve Bearing, 7mm OD | Misumi | MDZB5-6 | 8
5 | 5mm Oversize Thrust Bearing | Torque Transmisssion | MR-0512 | 12
7 | Knee Spring Anchor, 0.8mm thick steel | SendCutSend.com | | 2
8 | No Springs Tibya | CNCMadness.com | | 2
9 | No Springs Femur | CNCMadness.com | | 2
10 | No Springs Pogo Stick Center | CNCMadness.com | | 1
11 | Side Plate Minotaur | CNCMadness.com | | 2
12 | Minotaur Base Plate | CNCMadness.com | | 1
13 | M4 Shoulder Screw, 5mm shaft, 30mm long | McMaster-Carr | 90278A376 | 2
14 | M4 Locking Nut | McMaster-Carr | 93625A150 | 3
15 | Flanged Ball Bearing | McMaster-Carr | 57155K571 | 2
16 | Oil-Resistant Buna-N O-Ring | McMaster-Carr | 9262K342 | 2
17 | M3 Flathead Screw, 16mm long | McMaster-Carr | 92125A134 | 8
18 | M3 Buttonhead Screw, 8mm long | McMaster-Carr | 92095A181 | 4
19 | M3 Buttonhead Screw, 20mm long | McMaster-Carr | 92095A185 | 8
20 | M4 Shoulder Screw, 5mm shaft, 45mm Long | McMaster-Carr | 90278A507 | 1
21 | 1/4-20 Tapered Heat Set Insert | McMaster-Carr | 93365A160 | 2
22 | M3 Tapered Heat Set Insert | McMaster-Carr | 94180A331 | 4
23 | M4 Tapered Heat Set Insert | McMaster-Carr | 94180A351 | 2
24 | M5 Tapered Heat Set Insert | McMaster-Carr | 94180A361 | 21
25 | M5 Buttonhead Screw, 10mm long | McMaster-Carr | 92095A208 | 12
26 | 18-8 Stainless Steel Shoulder Screw | McMaster-Carr | 90265A126 | 2
27 | Pogo Center Tube Retainer | n/a, Laser Cut Delrin | | 2
28 | Foot Base | n/a, 3D Printed HTPLA | | 1
29 | Pogo Center Tabs | n/a, 3D Printed HTPLA | | 2

30 | Pogo Bearing Spacer | n/a, 3D Printed HTPLA | | 2

31 | Printed Knee Bumper | n/a, 3D Printed HTPLA | | 2

32 | M3 8mm Spacer | n/a, 3D Printed HTPLA | | 8

No-Spring Leg BOM

33 | M5, 16mm Threaded Foot | n/a, 3D Printed TPU | n/a | 1

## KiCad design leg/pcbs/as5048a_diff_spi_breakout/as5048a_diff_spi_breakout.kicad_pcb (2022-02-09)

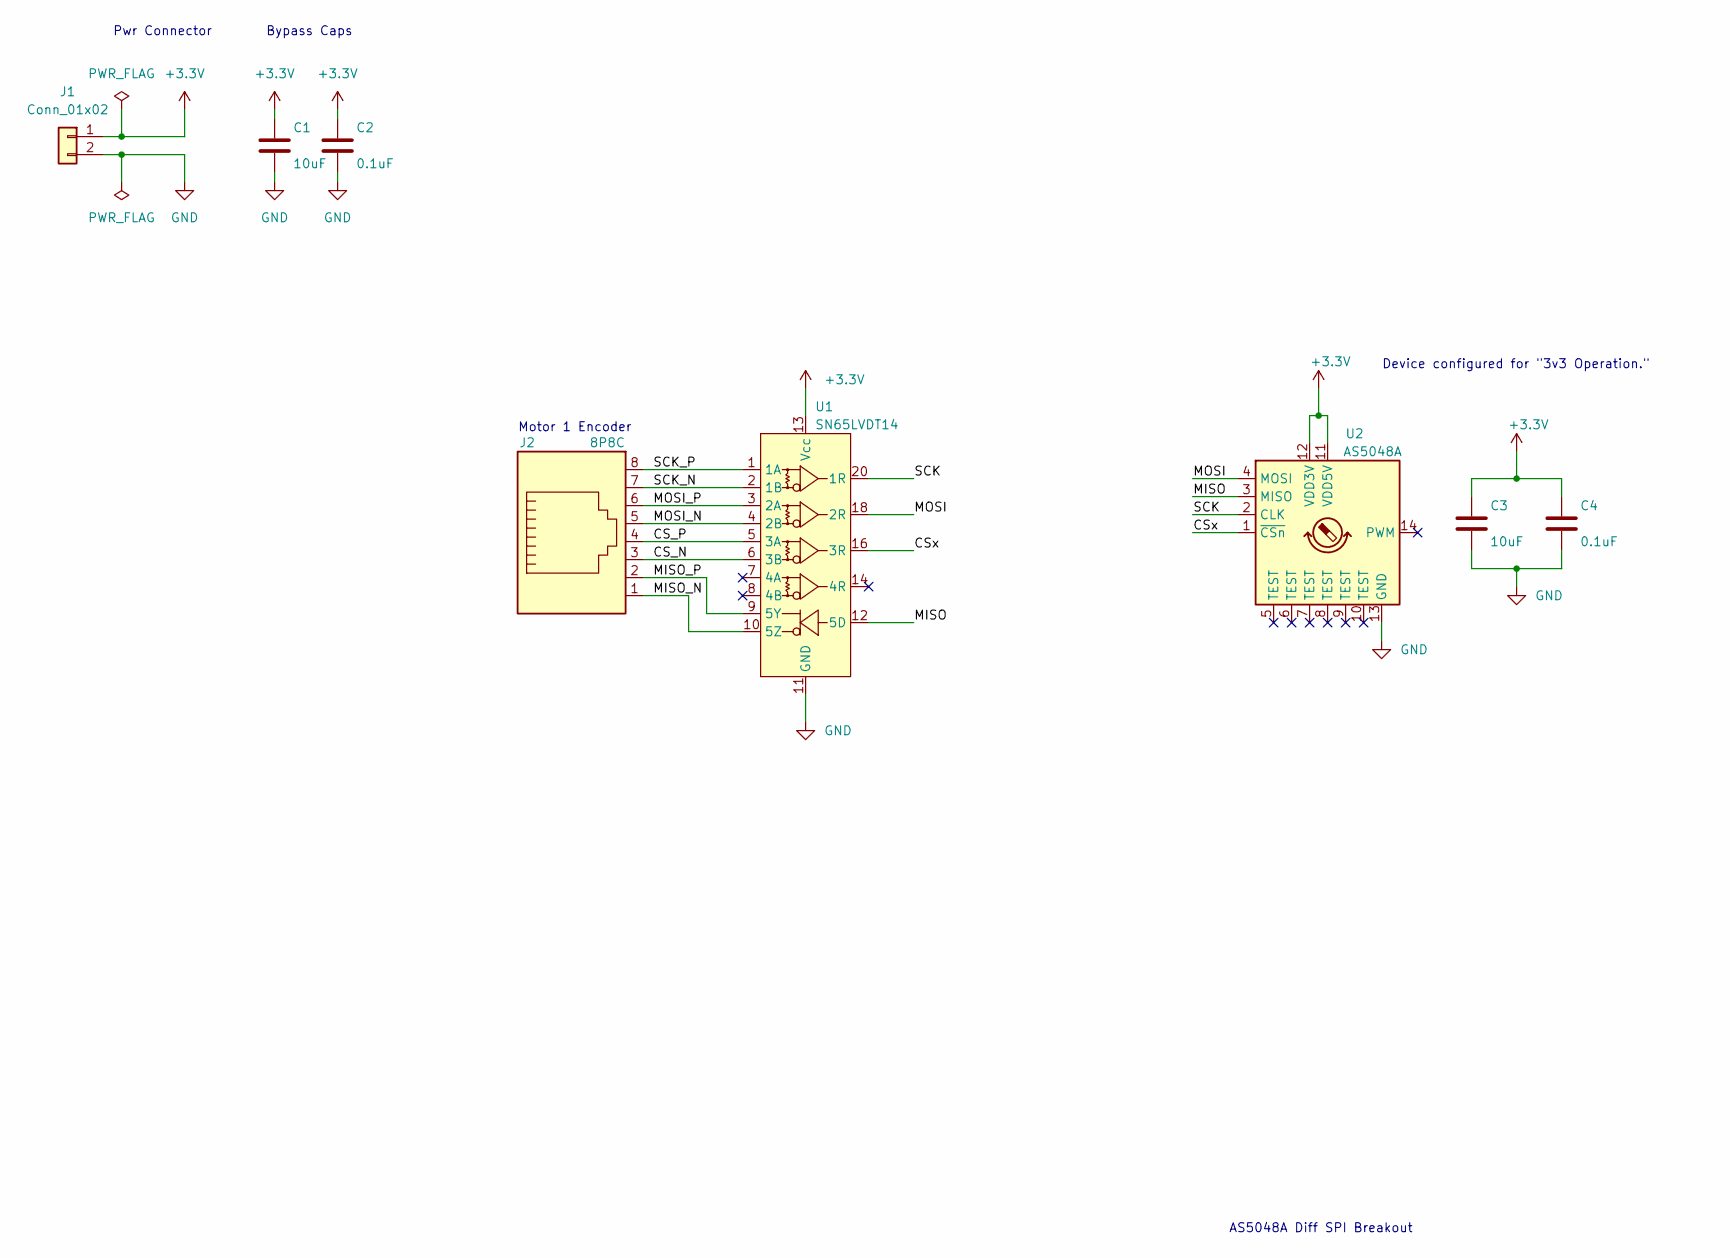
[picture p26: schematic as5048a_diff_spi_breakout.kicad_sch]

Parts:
C1, C3: 10uF; C_0603_1608Metric_Pad1.05x0.95mm_HandSolder
C2, C4: 0.1uF; C_0603_1608Metric_Pad1.05x0.95mm_HandSolder
J1: Conn_01x02; Molex_Micro-Fit_3.0_43650-0212_1x02_P3.00mm
J2: 8P8C; RJ45_Amphenol_SMD_RJSSE-5080-01T
U1: SN65LVDT14; TSSOP-20_4.4x6.5mm_P0.65mm
U2: AS5048A; TSSOP-14_4.4x5mm_P0.65mm

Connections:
+3V3: C1.1, C2.1, C3.1, C4.1, J1.1, U1.13 (Vcc), U1.17 (Vcc), U2.11 (VDD5V), U2.12 (VDD3V)
/CS_N: J2.3, U1.6 (3B)
/CS_P: J2.4, U1.5 (3A)
/CSx: U1.16 (3R), U2.1 (~CSn)
/MISO: U1.12 (5D), U2.3 (MISO)
/MISO_N: J2.1, U1.10 (5Z)
/MISO_P: J2.2, U1.9 (5Y)
/MOSI: U1.18 (2R), U2.4 (MOSI)
/MOSI_N: J2.5, U1.4 (2B)
/MOSI_P: J2.6, U1.3 (2A)
/SCK: U1.20 (1R), U2.2 (CLK)
/SCK_N: J2.7, U1.2 (1B)
/SCK_P: J2.8, U1.1 (1A)
GND: C1.2, C2.2, C3.2, C4.2, J1.2, U1.11 (GND), U1.15 (GND), U1.19 (GND), U2.13 (GND)

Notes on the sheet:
AS5048A Diff SPI Breakout
Pwr Connector
Motor 1 Encoder
Bypass Caps
Device configured for "3v3 Operation."

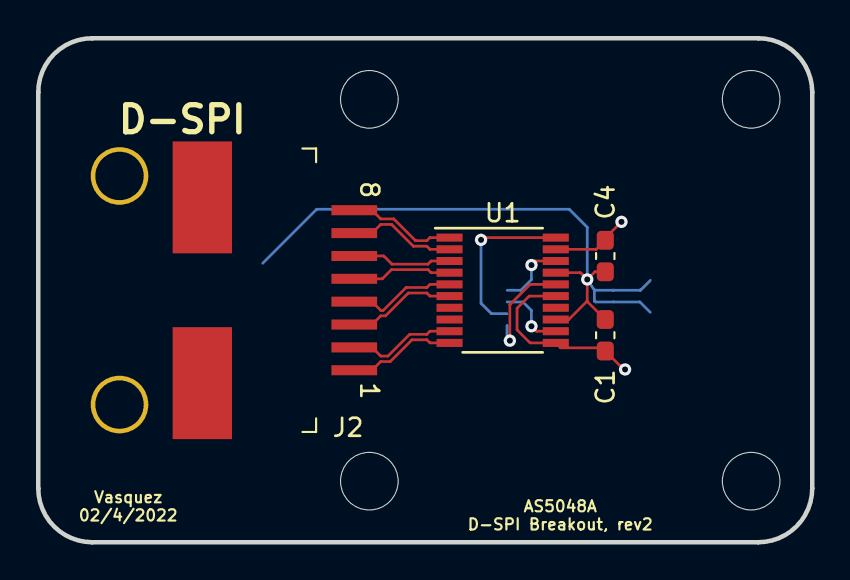
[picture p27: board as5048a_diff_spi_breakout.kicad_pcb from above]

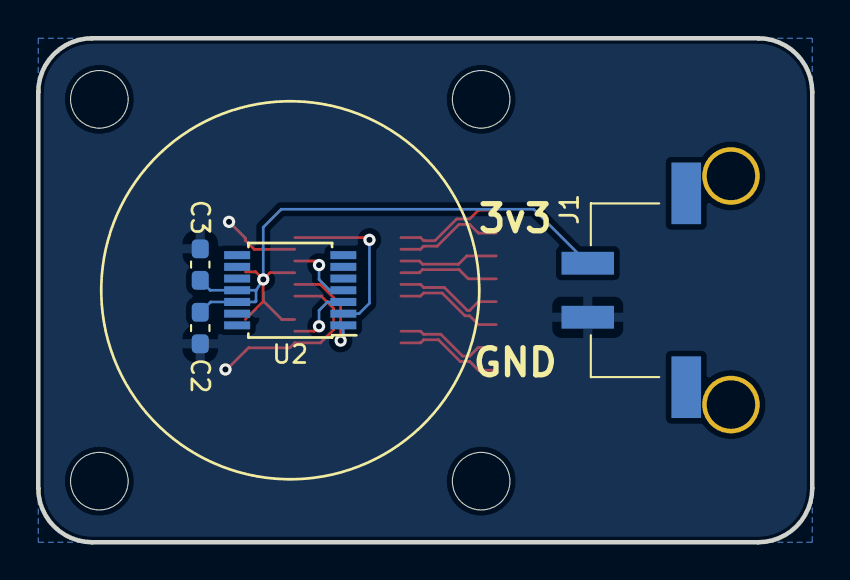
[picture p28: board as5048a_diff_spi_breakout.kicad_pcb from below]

Board: 2 copper layers, 43.0 x 28.0 mm, 8 parts (4 on the bottom side), 14 nets.

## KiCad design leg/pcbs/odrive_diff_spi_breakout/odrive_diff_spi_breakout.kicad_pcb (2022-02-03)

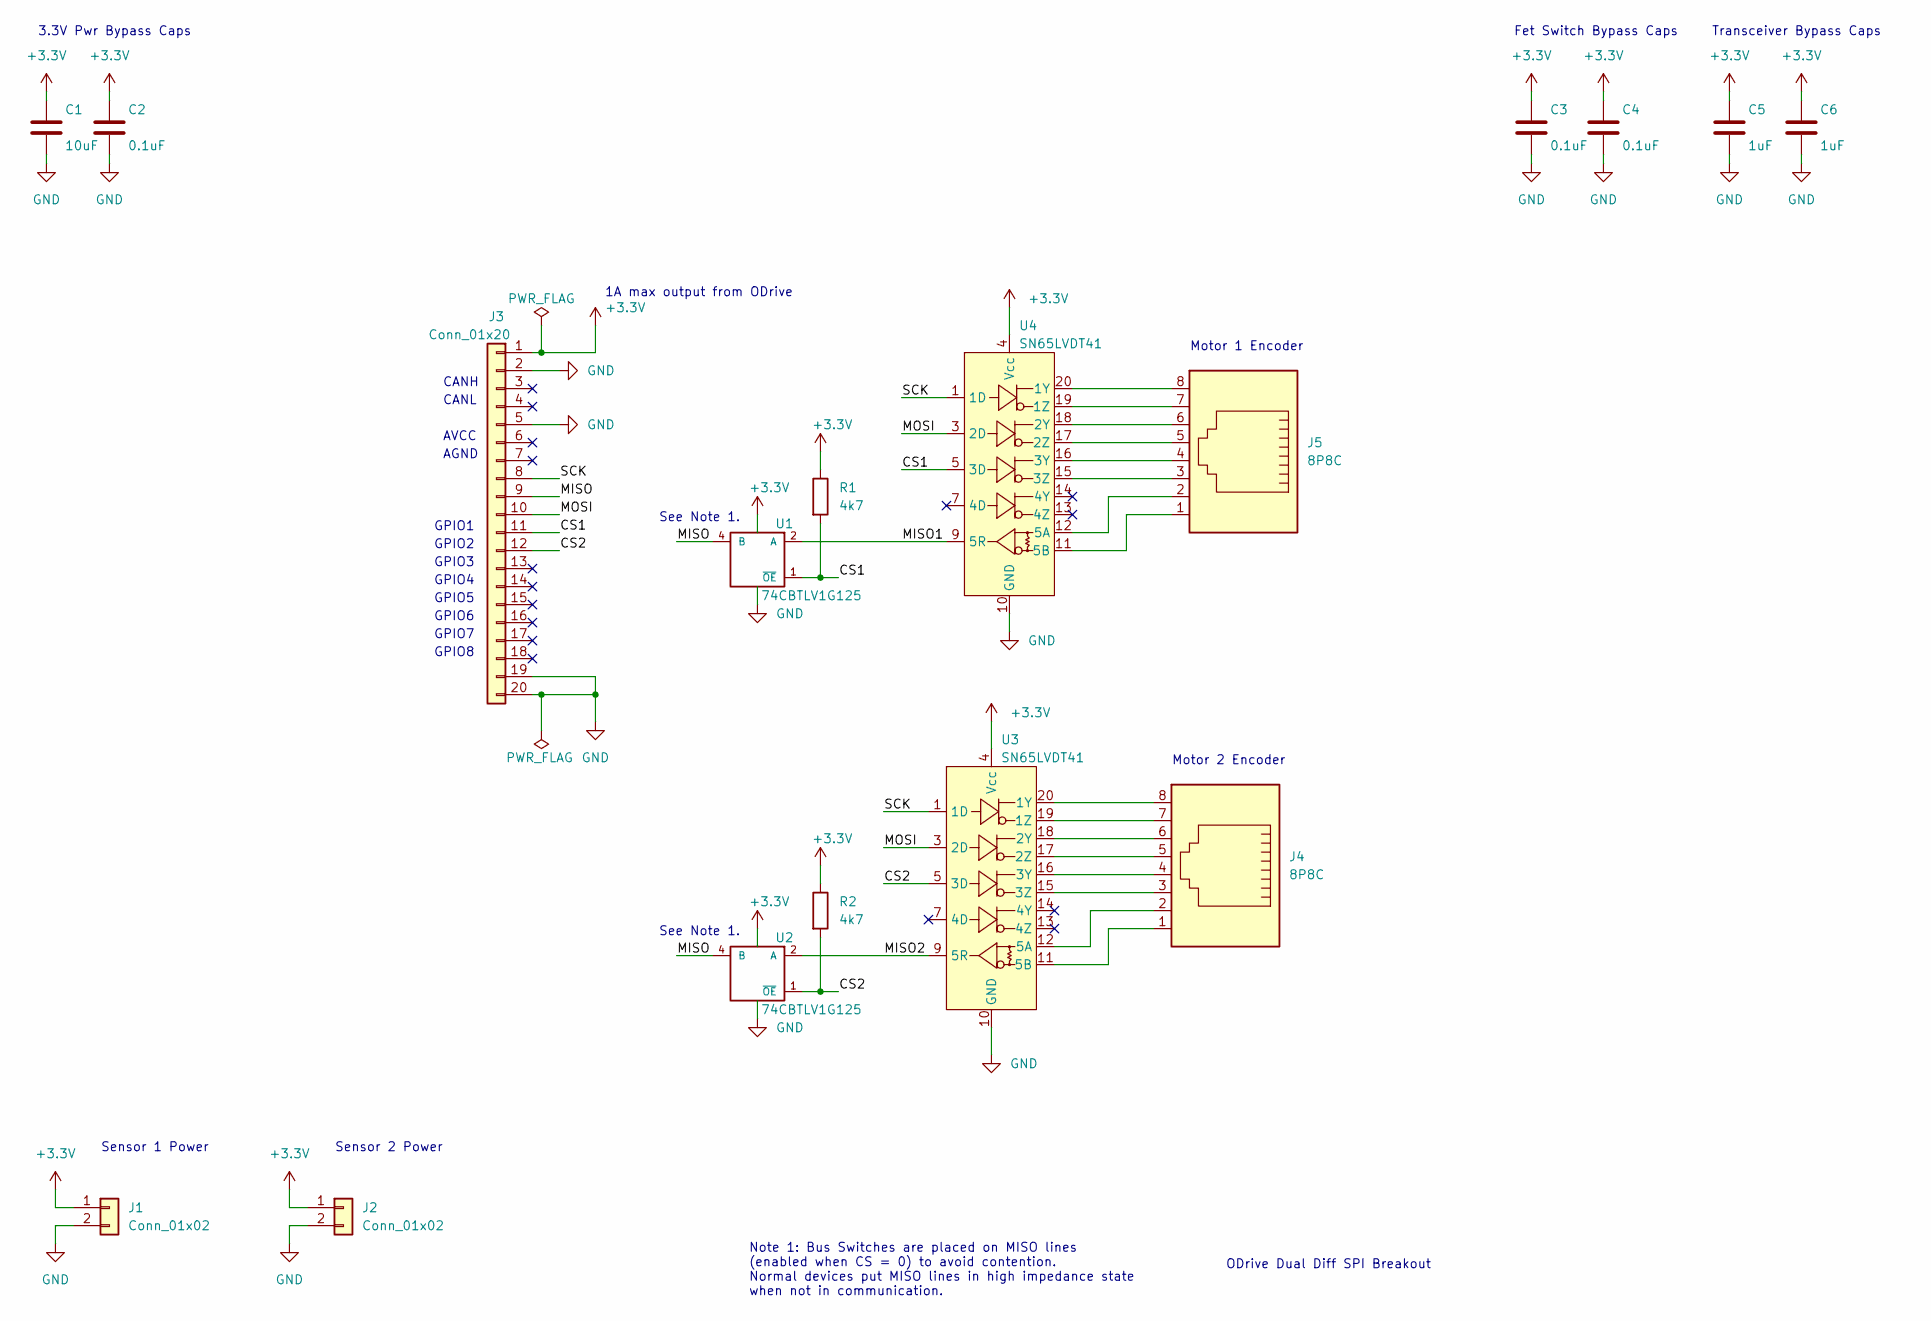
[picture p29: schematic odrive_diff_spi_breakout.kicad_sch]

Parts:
C1: 10uF; C_0603_1608Metric_Pad1.05x0.95mm_HandSolder
C2, C3, C4: 0.1uF; C_0603_1608Metric_Pad1.05x0.95mm_HandSolder
C5, C6: 1uF; C_0603_1608Metric_Pad1.05x0.95mm_HandSolder
J1, J2: Conn_01x02; Molex_Micro-Fit_3.0_43650-0215_1x02_P3.00mm_Vertical
J3: Conn_01x20; PinHeader_1x20_P2.54mm_Vertical
J4, J5: 8P8C; RJ45_Molex_SMD_0955036891
R1, R2: 4k7; R_0603_1608Metric_Pad1.05x0.95mm_HandSolder
U1, U2: 74CBTLV1G125; SOT-23-5_HandSoldering
U3, U4: SN65LVDT41; TSSOP-20_4.4x6.5mm_P0.65mm

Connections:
+3V3: C1.1, C2.1, C3.1, C4.1, C5.1, C6.1, J1.1, J2.1, J3.1, R1.1, R2.1, U1.5 (VCC), U2.5 (VCC), U3.4 (Vcc), U3.8 (Vcc), U4.4 (Vcc), U4.8 (Vcc)
/CS1: J3.11, R1.2, U1.1 (~OE), U4.5 (3D)
/CS2: J3.12, R2.2, U2.1 (~OE), U3.5 (3D)
/MISO: J3.9, U1.4 (B), U2.4 (B)
/MISO1: U1.2 (A), U4.9 (5R)
/MISO2: U2.2 (A), U3.9 (5R)
/MOSI: J3.10, U3.3 (2D), U4.3 (2D)
/SCK: J3.8, U3.1 (1D), U4.1 (1D)
GND: C1.2, C2.2, C3.2, C4.2, C5.2, C6.2, J1.2, J2.2, J3.2, J3.5, J3.19, J3.20, U1.3 (GND), U2.3 (GND), U3.2 (GND), U3.6 (GND), U3.10 (GND), U4.2 (GND), U4.6 (GND), U4.10 (GND)
unnamed: J4.1, U3.11 (5B)
unnamed: J4.2, U3.12 (5A)
unnamed: J4.3, U3.15 (3Z)
unnamed: J4.4, U3.16 (3Y)
unnamed: J4.5, U3.17 (2Z)
unnamed: J4.6, U3.18 (2Y)
unnamed: J4.7, U3.19 (1Z)
unnamed: J4.8, U3.20 (1Y)
unnamed: J5.1, U4.11 (5B)
unnamed: J5.2, U4.12 (5A)
unnamed: J5.3, U4.15 (3Z)
unnamed: J5.4, U4.16 (3Y)
unnamed: J5.5, U4.17 (2Z)
unnamed: J5.6, U4.18 (2Y)
unnamed: J5.7, U4.19 (1Z)
unnamed: J5.8, U4.20 (1Y)

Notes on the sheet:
ODrive Dual Diff SPI Breakout
GPIO8
1A max output from ODrive
GPIO3
3.3V Pwr Bypass Caps
AGND
GPIO5
CANL
Motor 2 Encoder
AVCC
Sensor 1 Power
Motor 1 Encoder
See Note 1.
GPIO6
GPIO1
CANH
GPIO2
Note 1: Bus Switches are placed on MISO lines (enabled when CS = 0) to avoid contention. Normal devices put MISO lines in high impedance state when not in communication.
GPIO4
Sensor 2 Power
Transceiver Bypass Caps
GPIO7
Fet Switch Bypass Caps

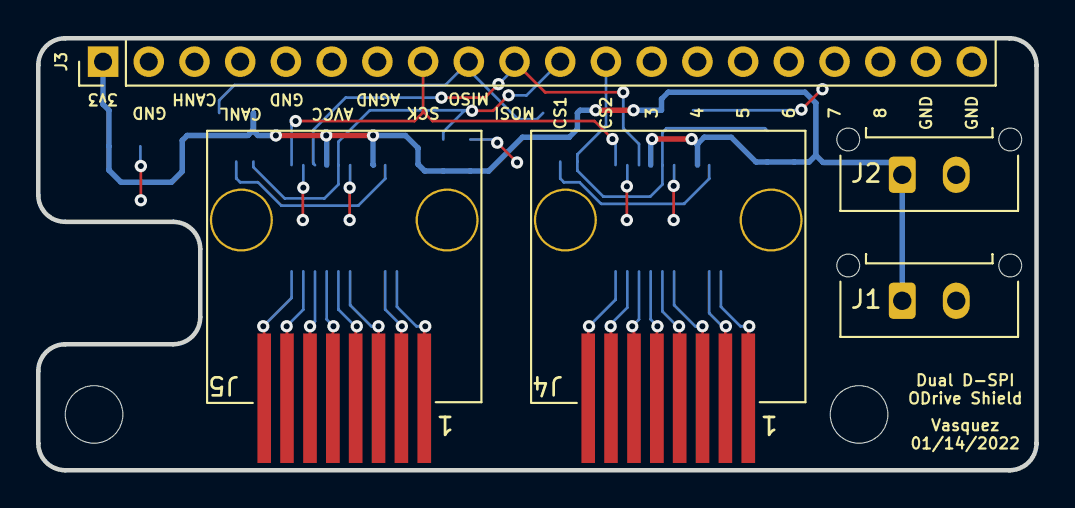
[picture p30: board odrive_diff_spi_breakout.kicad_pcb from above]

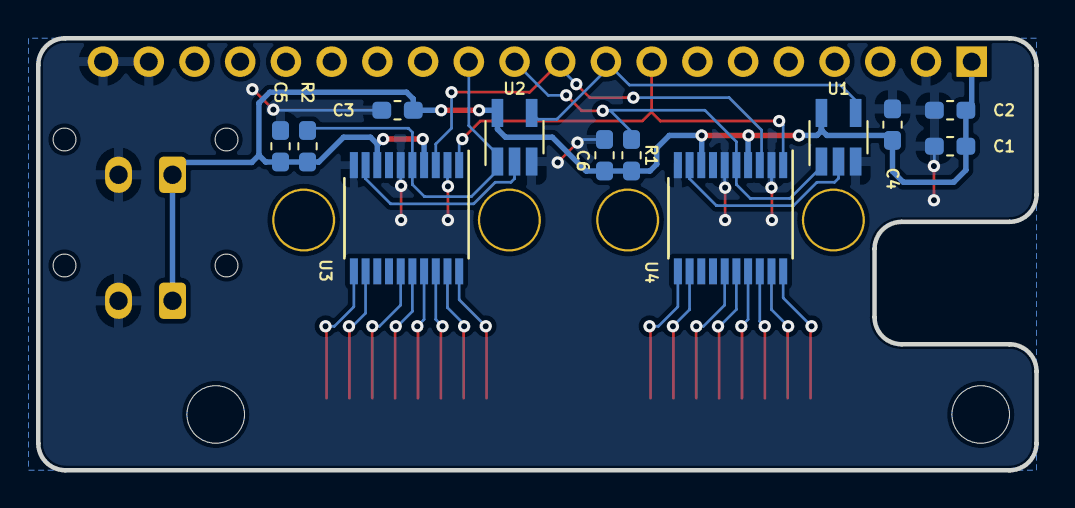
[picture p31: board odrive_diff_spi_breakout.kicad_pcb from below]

Board: 2 copper layers, 55.5 x 24.0 mm, 17 parts (12 on the bottom side), 25 nets.

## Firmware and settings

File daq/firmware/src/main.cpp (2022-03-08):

#include <libopencm3/stm32/rcc.h>
#include <libopencm3/stm32/gpio.h>
#include <libopencm3/usb/usbd.h>
#include <libopencm3/cm3/nvic.h> // for otg_fs_isr and other isr's
#include <libopencm3/stm32/timer.h>  // for timer constants.
#include <usbd_setup.h>
#include <analog_input.h>
#include <millis.h>
#include <stdlib.h>


// TODO: abstract all of this USB buffering junk into a small class
// with pointers to writing buffers ping and pong.

// ------ Overview: ------
// Define a Packet structure such that we can send multiple datapoints over
// to the PC with one USB packet transfer (64 bytes).
// Create a Ping-Pong Buffer to aggreggate datapoints in one packet while
// writing out the other one over USB.
// Setup a timer to define our sampling frequency (~ 1 KHz).
// In the main loop,
// -- check if it's time to read new sample data over SPI (as set by the timer).
// -- check if we've filled up a usb packet. If so, switch buffers and
//    dispatch the full packet.


// ------ Constants: ------
static const size_t DEFAULT_SAMPLING_FREQ = 5000; // [Hz]
static const size_t DATAPTS_PER_PKT = 30; // number of samples in a USB packet.


// ------ Structure Definitions: ------
// Define structure of the USB Packet that will transfer the analog data.
#pragma pack(push, 1) // Tell compiler we want an exact fit without padding.
struct usb_packet // use pragma to enforce packet size of 64 bytes.
{
    uint16_t analog_time_series[DATAPTS_PER_PKT]; // 60 bytes
    uint32_t packet_index; // 4 bytes
};
#pragma pack(pop)

// Create some system-wide flags to manage control flow.
struct state_flags
{
    bool adc_read_pending; // Flag to indicate when to read new analog data.
    bool usb_output_data_ready; // Flag to indicate when to write usb packet.
};

// ------ Variables and Structures: ------
volatile state_flags system_state{false, false}; // mark volatile since ISRs will modify it.

// Ping-Pong Buffers for aggregating analog data.
// Write to one while transferring the other. Then swap.
usb_packet ping;
usb_packet pong;
// Pointers to demarcate who is being written-to and who is being transferred.
usb_packet* sampling_buffer;
usb_packet* usb_writing_buffer;

// A packet ID that increments once per stuffed packet.
// Note that packets can fly as fast as 1KHz on Full Speed, so this value
// should be sufficiently large to ID packets before rollover.
uint32_t usb_sent_pkts_index = 0;
// Index into the packet to determine where to write next.
uint8_t usb_pkt_datapt_index = 0;


// ------ Functions: ------
// Callback fn for handling usb control transfers.
// Change the sampling freq over USB.
static enum usbd_request_return_codes simple_control_cb(
        usbd_device *usbd_dev, struct usb_setup_data *req, uint8_t **buf,
		uint16_t *len, void (**complete)(usbd_device *usbd_dev, struct usb_setup_data *req))
{
	(void)buf;
	(void)len;
	(void)complete;
	(void)usbd_dev;

    // Ignore all other requests besides a Vendor Request type.
	if (req->bmRequestType != 0x40) // Vendor Request
		return USBD_REQ_NOTSUPP;

    // TODO: setup callback to change the sample frequency
	if (req->wValue & 1)
		gpio_set(GPIOB, GPIO7);
	else
		gpio_clear(GPIOB, GPIO7);

	return USBD_REQ_HANDLED;
}


static void usb_set_config_cb(usbd_device *usbd_dev, uint16_t wValue)
{
	(void)wValue;

    // Setup bulk transfer output.
    usbd_ep_setup(usbd_dev, 0x81, USB_ENDPOINT_ATTR_BULK, 64, NULL);
    // Callback fn for handling data from a received control transfer.
	usbd_register_control_callback(
				usbd_dev,
				USB_REQ_TYPE_VENDOR,
				USB_REQ_TYPE_TYPE,
				simple_control_cb);
}


// Set sampling frequency at values between 15.26[Hz] and 1[MHz]
// not all frequencies are possible.
// Pause and re-enable TIM7 interrupt by default unless told to ignore.
void set_sampling_freq(uint32_t hz, bool ignore_irq_state = false)
{
    uint32_t ticks = 1e6/hz; // Note: timer is set to tick at 1 [MHz].
    // 1 tick for 1[MHz]. 1000 ticks for 1[KHz]. 4000 ticks for 250[Hz]. etc.
    // eqn is: UPDATE_FREQ = TICK_RATE / PERIOD
    if (!ignore_irq_state)
        nvic_disable_irq(NVIC_TIM7_IRQ);
    timer_set_period(TIM7, ticks);
    if (!ignore_irq_state)
        nvic_enable_irq(NVIC_TIM7_IRQ); // re-enable interrupt.
}


// Setup trigger interval for Timer7 interrupt.
// This ISR dictates the sample rate.
void setup_sampling_timer(void)
{
    rcc_periph_clock_enable(RCC_TIM7);
    nvic_enable_irq(NVIC_TIM7_IRQ);
    rcc_periph_reset_pulse(RST_TIM7); // reset timer 7 to defaults.

// Primary Datasheet for STM32F415xx Sec 2.2, Fig 5 has clock APB mapping.
// RM0090 Manual for Sec 7.2, Fig 21 has the clock tree (prescaling) mapping.
// TIM7 uses APB1.
// For current clock (rcc) settings, we have:
// AHB --> no prescaling
// APB1 --> DIV4
// CLK_INT --> 168000000 / 4 x 2 = 84 [MHz]

    timer_set_mode(TIM7,
                   TIM_CR1_CKD_CK_INT, // No additional clock division ratio.
                   TIM_CR1_CMS_EDGE, // Edge alignment.
                   TIM_CR1_DIR_UP); // Up-counting counter

    timer_set_prescaler(TIM7, 84); // Increment at 1[MHz]
    set_sampling_freq(DEFAULT_SAMPLING_FREQ, true); // don't alter irq state.
    timer_disable_preload(TIM7);
	timer_continuous_mode(TIM7);
    timer_enable_counter(TIM7);

    // When the timer updates, the interrupt should fire.
    timer_enable_irq(TIM7, TIM_DIER_UIE); // Timer 7 update interrupt enable.
}


// Handle usb activity via ISR so we don't have to poll it in the main loop.
// this fn is weakly defined in NVIC.h
void otg_fs_isr(void)
{
   usbd_poll(usbd_dev);
}

// ISR to sample the data and transfer it into ping-pong buffer.
// this fn is weakly defined in NVIC.h
void tim7_isr(void)
{
    timer_clear_flag(TIM7, TIM_SR_UIF);
    gpio_toggle(GPIOA, GPIO8);
    system_state.adc_read_pending = true;
}


// Read the analog input data
// Flag if the usb data is full and ready for transfer.
void sample_and_store_datapt(void)
{
    sampling_buffer->analog_time_series[usb_pkt_datapt_index] =
        read_adc_naiive(ADC1, 8); // PB0 is ADC1_IN8.

    // Increment to the next datapt.
    ++usb_pkt_datapt_index;
}

// Check if we've filled up the buffer we're writing to.
// Flag if we need to dispatch usb packet.
void handle_usb_buffers(void)
{
    // Check buffer index. Switch buffers if necessary.
    if (usb_pkt_datapt_index > DATAPTS_PER_PKT - 1)
    {
        /// Setup writing at the beginning of the next packet.
        usb_pkt_datapt_index = 0;
        // ID the packet before transmitting so we can sort them on the receiving end.
        sampling_buffer->packet_index = usb_sent_pkts_index;
        // Swap buffers.
        usb_writing_buffer = sampling_buffer;
        sampling_buffer = (sampling_buffer == &ping)? &pong: &ping;
        // Flag that we are ready to transfer USB data in the main loop.
        system_state.usb_output_data_ready = true;
        // Move on to the next packet.
        ++usb_sent_pkts_index;
    }
}


// ------ main thread: ------
int main(void)
{
    setup_system_clock(); // do this first.
    setup_systick(); // for delay_ms fn

    // Enable GPIO for a Blinky.
	rcc_periph_clock_enable(RCC_GPIOB);
    // enable GPIOA for usb-related GPIO.
	rcc_periph_clock_enable(RCC_GPIOA);

    // encoder counting and sampling setup:
    setup_sampling_timer();

    // USB init.
	rcc_periph_clock_enable(RCC_OTGFS);


	// Setup 1bity's status LED for output.
	gpio_mode_setup(GPIOA, GPIO_MODE_OUTPUT, GPIO_PUPD_NONE, GPIO8);

    // Relevant Pinouts:
    // PA8 --> USB SOF (start of frame, unused)
    // PA9 --> USB Vbus (otg fs VBus sensing, unused, disabled)
    // PA10 --> USB ID (otg fs id)
    // PA11 --> USB DM (Data minus)
    // PA12 --> USB DP (Data plus)
    // PG6 --> USB GPIO OUT (unused)
    //gpio_mode_setup(GPIOA, GPIO_MODE_AF, GPIO_PUPD_NONE, GPIO10 | GPIO11 | GPIO12);
    //gpio_set_af(GPIOA, GPIO_AF10, GPIO10 | GPIO11 | GPIO12);
    gpio_mode_setup(GPIOA, GPIO_MODE_AF, GPIO_PUPD_NONE, GPIO11 | GPIO12);
    gpio_set_af(GPIOA, GPIO_AF10, GPIO11 | GPIO12);

    // Setup interrupts for handling usb events.
    nvic_enable_irq(NVIC_OTG_FS_IRQ);

	usbd_dev = usbd_init(&otgfs_usb_driver, &dev, &config,
                         usb_strings, 3,
                         usbd_control_buffer, sizeof(usbd_control_buffer));
	usbd_register_set_config_callback(usbd_dev, usb_set_config_cb);

    setup_adc(ADC1);
    setup_gpio_for_adc(GPIOB, 0); // PB0 is ADC1_IN8.


    // Main Loop: Check if it's time to write the packet, and write it.
    // tim7_isr flags for any of these behaviors to execute.
    // Note: we assume that a USB packet transfer happens faster than it takes
    //       to fill the usb buffer.
    // Note: We assume that these combined behaviors execute and complete
    //       before it's time to execute them again.
	while (1)
    {
		//usbd_poll(usbd_dev); // not needed since we're using interrupts.
        if (system_state.adc_read_pending)
        {
            system_state.adc_read_pending = false; // Clear the flag.
            sample_and_store_datapt(); // read adc data and store it in packet.
            handle_usb_buffers(); // Switch PingPong buffers. Flag for sending.
        }

        if (system_state.usb_output_data_ready)
        {
            system_state.usb_output_data_ready = false; // Clear the flag.
            // Cast the struct into a serialized sequence of bytes.
            usbd_ep_write_packet(usbd_dev, 0x81, (const void*)usb_writing_buffer,
                                 BULK_BUFFER_SIZE);
            //gpio_toggle(GPIOA, GPIO8);
        }
    }

}

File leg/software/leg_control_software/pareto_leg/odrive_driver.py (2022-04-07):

#!/usr/bin/env python3
"""Driver for controlling both ODrive axes."""
from inpromptu import Inpromptu, cli_method

from math import pi

from odrive.utils import dump_errors
from odrive.enums import *
import odrive


#class OdriveDriver(object):
class OdriveDriver(Inpromptu):

    def __init__(self, odrive):
        """constructor.

        Assumes odrives have already been configured according to the bringup
        script."""
        super().__init__()
        self.od = odrive
        self.control_mode = None
        self.reset()


    @cli_method
    def reset(self):
        """initialize the motors."""
        self.od.clear_errors()
        self.set_position_control_mode()
        self.od.axis0.controller.config.input_mode = INPUT_MODE_PASSTHROUGH
        self.od.axis1.controller.config.input_mode = INPUT_MODE_PASSTHROUGH
        self.disarm()


    @cli_method
    def arm(self):
        """Arm the leg motors."""
        self.od.axis0.requested_state = AXIS_STATE_CLOSED_LOOP_CONTROL
        self.od.axis1.requested_state = AXIS_STATE_CLOSED_LOOP_CONTROL


    @cli_method
    def disarm(self):
        """disarm the leg motors."""
        self.od.axis0.requested_state = AXIS_STATE_IDLE
        self.od.axis1.requested_state = AXIS_STATE_IDLE


# Modes:
    def set_mode(self, mode):
        self.od.axis0.controller.config.control_mode = mode
        self.od.axis1.controller.config.control_mode = mode


    @cli_method
    def set_position_control_mode(self):
        """Wrapper for setting position control mode."""
        self.set_mode(CONTROL_MODE_POSITION_CONTROL)
        self.control_mode = CONTROL_MODE_POSITION_CONTROL


    @cli_method
    def set_torque_control_mode(self):
        """Wrapper for setting torque control mode."""
        self.set_mode(CONTROL_MODE_TORQUE_CONTROL)
        self.control_mode = CONTROL_MODE_TORQUE_CONTROL


# Homing:
    @cli_method
    def zero_position(self):
        """Set the current position as (0,0)"""
        try:
            self.od.axis0.encoder.set_linear_count(0)
            self.od.axis1.encoder.set_linear_count(0)
        except Exception as e:
            print(e.message)
            dump_errors(self.od)


# Position and Torque Control Read and Writes:
    @cli_method
    def set_torques(self, axis0_torque: float, axis1_torque: float):
        """set the torque on both motors in [Amps].
           Print message if we needed to switch modes first. Catch
           motor-related exceptions."""

        if self.control_mode != CONTROL_MODE_TORQUE_CONTROL:
            print("Switching to Torque Control Mode.")
            self.set_torque_control_mode()

        try:
            self.od.axis0.controller.input_torque = axis0_torque
            self.od.axis1.controller.input_torque = axis1_torque
        except Exception as e:
            print(e.message)
            dump_errors(e)


    @cli_method
    def get_torques(self):
        """Read both torques."""
        return (self.od.axis0.motor.current_control.Iq_measured,
                self.od.axis1.motor.current_control.Iq_measured)


    def set_motor_angles(self, axis0_angle_rad, axis1_angle_rad):
        """Set the angles of both motors in radians.
           Print message if we needed to switch modes first. Catch
           motor-related exceptions."""

        if self.control_mode != CONTROL_MODE_POSITION_CONTROL:
            print("Switching to Position Control Mode.")
            self.set_position_control_mode()

        try:
            # Convert radians to revolutions.
            self.od.axis0.controller.input_pos = axis0_angle_rad / (2 * pi)
            self.od.axis1.controller.input_pos = axis1_angle_rad / (2 * pi)
        except Exception as e:
            print(str(e))
            print("ODrive Status Dump:")
            dump_errors(self.od)


    @cli_method
    def set_motor_angles_deg(self, axis0_angle_deg: float, axis1_angle_deg: float):
        return self.set_motor_angles(axis0_angle_deg * (pi/180),
                                     axis1_angle_deg * (pi/180))


    @cli_method
    def get_motor_angles(self):
        """Read both angles (in radians) from each odrive axis.

        Note: looking top-down at the motor, CCW rotation is positive on each motor.
        Note: Angles (radians) are not clamped and not calibrated.

        """
        # *.pos_estimate is the estimated angle after running through the
        # state observer to correct encoder phase lag.
        return (self.od.axis0.encoder.pos_circular* 2 * pi,
                self.od.axis1.encoder.pos_circular* 2 * pi)


    @cli_method
    def get_motor_velocities(self):
        """Read both angle velocities (in radians) from each odrive axis.

        Note: looking top-down at the motor, CCW rotation is positive on each motor.

        """
        # *.pos_estimate is the estimated angle after running through the
        # state observer to correct encoder phase lag.
        return (self.od.axis0.encoder.vel_estimate * 2 * pi,
                self.od.axis1.encoder.vel_estimate * 2 * pi)


    def configure_motor_angles_as(self, axis0_angle_rad: float, axis1_angle_rad: float):
        """Set the current motor angles to be a specific value in radians."""

        axis0_cpr = self.od.axis0.encoder.config.cpr
        axis1_cpr = self.od.axis1.encoder.config.cpr

        curr_pos_rad = self.get_motor_angles()

        #new_angle_rad = [curr_pos_rad[0] + axis0_angle_rad,
        #                 curr_pos_rad[1] + axis1_angle_rad]
        new_angle_rad = [axis0_angle_rad,
                         axis1_angle_rad]

        # Clamp above values to (-pi, +pi)
        for index, angle in enumerate(new_angle_rad):
            while new_angle_rad[index] < -pi:
                new_angle_rad[index] += 2*pi
            while new_angle_rad[index] > pi:
                new_angle_rad[index] -= 2*pi

        self.od.axis0.encoder.set_linear_count(new_angle_rad[0]/(2*pi)*axis0_cpr)
        self.od.axis1.encoder.set_linear_count(new_angle_rad[1]/(2*pi)*axis1_cpr)


    @cli_method
    def configure_motor_angle_degs_as(self, axis0_angle_deg: float, axis1_angle_deg: float):
        self.configure_motor_angles_as(axis0_angle_deg * (pi/180),
                                       axis1_angle_deg * (pi/180))


    @cli_method
    def dump_errors(self):
        """Dump axis0 and axis1 errors."""
        dump_errors(self.od)


if __name__ == "__main__":

    odrv0 = odrive.find_any()
    my_odd = OdriveDriver(odrv0)

    my_odd.cmdloop()

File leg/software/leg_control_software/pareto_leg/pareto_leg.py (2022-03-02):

#!/usr/bin/env python3
"""Driver for controlling leg position"""
from inpromptu import Inpromptu, cli_method

from .five_bar_kins import FiveBarKinematics2D
from .odrive_driver import OdriveDriver
import odrive


class ParetoLeg(Inpromptu):
#class ParetoLeg(object):

    # constants
    CALIB_ANGLE_DEGS = [90, 90]


    def __init__(self, odrive, l1_len, l2_len):
        """constructor. Assumes odrive motors have already been pre-configured."""
        super().__init__()
        self.odd = OdriveDriver(odrive)
        self.kins = FiveBarKinematics2D(l1_len, l2_len)


    def set_cartesian_position(self, x, y):
        """Set the position of the robot leg in cartesian coordinates."""
        theta_axis0, theta_axis1 = self.kins.cartesian_to_joint(x, y)
        # Kinematic model assumes flipped angle0 from how it is installed
        # based on leg configuration.
        theta_axis0 = -theta_axis0
        self.odd.set_positions(theta_axis0, theta_axis1)


    @cli_method
    def get_cartesian_position(self):
        """Get the position of the robot leg in cartesian coordinates."""
        theta_axis0, theta_axis1 = self.odd.get_motor_angles() # radians.
        return self.kins.joint_to_cartesian([theta_axis0, theta_axis1])


    @cli_method
    def get_joint_angles(self):
        """Get the angular position of each joint according to configuration assumptions.

        Note: with robot orientation is Motor0 closer to Motor1, both motor
              angles are positive when the leg moves CCW in this orientation.

        """
        motor_angles = self.odd.get_motor_angles()
        # Handle Joey configuration convention.
        return (-motor_angles[0], motor_angles[1])


    def set_joint_angles(self, motor0_theta, motor1_theta):
        """Set the angular position of each joint according to configuration assumptions.

        Angle units are in radians.
        """
        self.odd.set_motor_angles(-motor0_theta, motor1_theta)


    @cli_method
    def apply_calibration(self):
        """Tell the ODrive that the current position is the calibration position."""

        # Configure the motor in joint space.
        # i.e: CCW rotation is positive angle looking top-down at each motor.
        self.odd.configure_motor_angle_degs_as(ParetoLeg.CALIB_ANGLE_DEGS[0],
                                               ParetoLeg.CALIB_ANGLE_DEGS[1])


    def get_joint_velocities(self):
        """Get the angular velocity of each joint."""
        pass # TODO!

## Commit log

2022-01-23 rev1 of pcbs finished
    [as5048a_diff_spi_breakout.kicad_pcb, as5048a_diff_spi_breakout.kicad_sch, odrive_diff_spi_breakout.kicad_pcb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]
2022-01-26 motor configuration figured out
2022-01-28 config for one motor looks good
2022-02-09 adding pareto leg kins
    [as5048a_diff_spi_breakout.kicad_pcb, as5048a_diff_spi_breakout.kicad_sch]
2022-02-10 folder re-org
    [as5048a_diff_spi_breakout.kicad_pcb, as5048a_diff_spi_breakout.kicad_sch, odrive_diff_spi_breakout.kicad_pcb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]
2022-02-12 updating driver
2022-02-18 folder restructure
    [as5048a_diff_spi_breakout.kicad_pcb, as5048a_diff_spi_breakout.kicad_sch, odrive_diff_spi_breakout.kicad_pcb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]
2022-02-18 writing motor script for provisioning two motors
2022-02-18 adding motor angle get/set funcs
2022-02-28 adding bringup script for commissioning a fresh leg
2022-03-01 directory reorg
    [odrive_diff_spi_breakout.kicad_sch]
2022-03-08 demystifying timer update rate
2022-03-09 adding some print output for daq
2022-03-10 adding test file for reading motor angles.
2022-03-14 adding cad model
    [4mm_sleeve_bearing_3mm_long_8mm_od_6658K114.SLDPRT, 5mm_sleeve_bearing_4mm_long_8mm_od_6658K116.SLDPRT, 5mm_sleeve_bearing_6mm_long_7mm_od_MDZB5-6.SLDPRT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]
2022-03-22 Add files via upload
    adding knee assembly doc
2022-03-24 oodles of changes, including fixed wrapping my my_odd. TODO update all experiment scripts
    [odrive_driver.py, stream_motor_angles.py]
2022-03-24 actually, still trying to fix the motor angle wrapping but. Experiment scripts are TODO
    [odrive_driver.py, stream_motor_angles.py]
2022-03-24 updated example_julia_commpunication.py script to handle new motor calibration measurements
2022-03-31 updating odrive branch
2022-03-31 updating motor bringup docs
2022-04-01 adding stls in printing orientations
    [8mm_m3_spacer.STL, base_plate.STL, base_plate_no_knee_springs.STL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]
2022-04-01 adding print list
2022-04-07 joey pushing lots of software changes, most lab experiment scripts are still broken
    [odrive_driver.py, stream_motor_angles.py]
2022-04-16 major changes to leg cad
    [4mm_sleeve_bearing_3mm_long_8mm_od_6658K114.SLDPRT, 5mm_sleeve_bearing_4mm_long_8mm_od_6658K116.SLDPRT, 5mm_sleeve_bearing_6mm_long_7mm_od_MDZB5-6.SLDPRT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]
2022-04-16 major rework of cad in progress
    [Femur V5.SLDPRT, Full Robot Assembly V5.SLDASM, Knee Anchor Loop.SLDPRT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]
2022-05-02 update to solidworks design files for version 5 of pareto leg
    [Femur V5.SLDPRT, Full Robot Assembly V5.SLDASM, Knee Anchor Loop.SLDPRT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]
2023-02-17 major update post summer 2022
    [foo.csv, motor_axis_config.yaml]
